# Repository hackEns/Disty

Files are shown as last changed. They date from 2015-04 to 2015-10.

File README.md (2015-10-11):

Disty
=====

Disty is a [hackEns](http://hackens.org) project by [Phyks](http://phyks.me)
and [Elie](http://exppad.com/) aiming at building a low-cost telepresence robot
for videoconference.

More infos can be found on the [project page](http://hackens.org/disty) (in
French). The README and the source code is another good source of
documentation, which should be self-explanatory, in English.

This repo contains all the drawings and code we used to make it work.

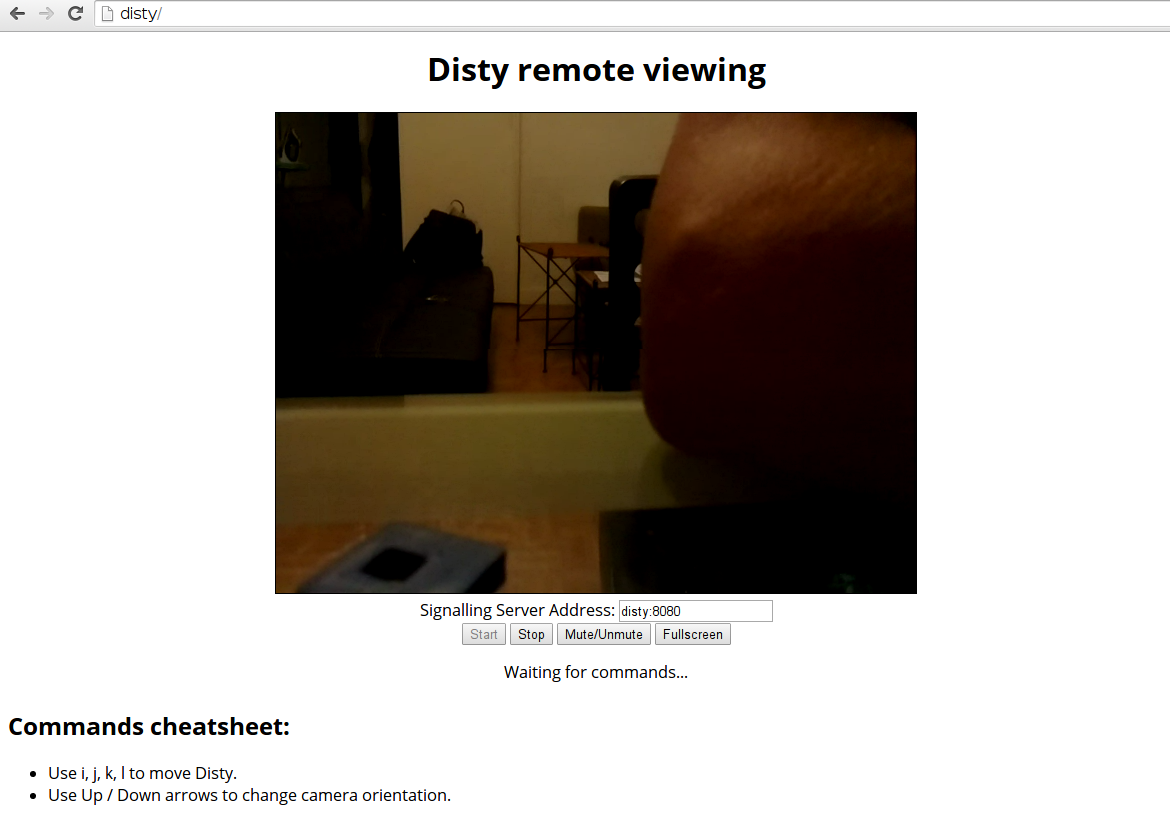
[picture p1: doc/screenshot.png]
Screen capture


<hr/>

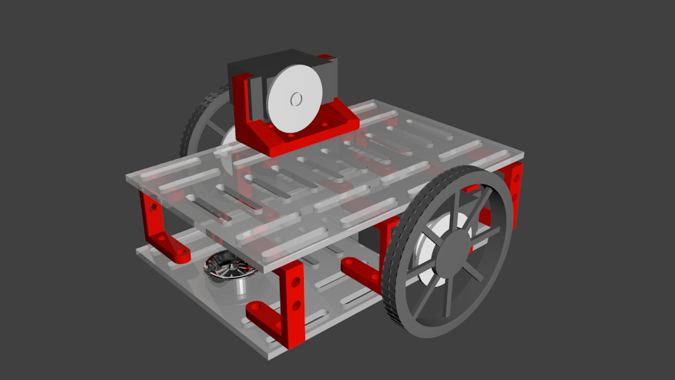
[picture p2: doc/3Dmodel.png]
3D model


<hr/>

Disty

Disty

Disty

## Content of this repo

* `blueprints` contains all the blueprints and drawings for this project.
* `disty` contains the main C++ code, responsible for handling Disty movements
and basic operations.
* `webview` contains the code for the webview, which is the web interface used
to control Disty and display camera (for the remote user).

Note that these folders also contain useful READMEs with more detailed
information on them.

Blueprints are either in `eps` (ready to cut files) or `svg` (working files).
These should be the same and both are provided only to ease usage and
modifications. STL files are ready to print files. They should be included in
the Blender blend files, for easy modifications.

You should laser cut the `top` and `bottom` files for the two main plates.
You should 3D print:
* the `picam_case_*` files for the camera case (licensed under CC BY SA).
* `teleprez.blend` is the complete CAO model of the robot in Blender.
* `camera_servo_holder.stl` is the plastic part to hold the camera servo. You
need to print it once (with a 10,000 scale factor).
* `wheel_servo_holder.stl` is the plastic part to hold the servos for the
wheels. You need four of them (with a 10,000 scale factor).

## Wiring

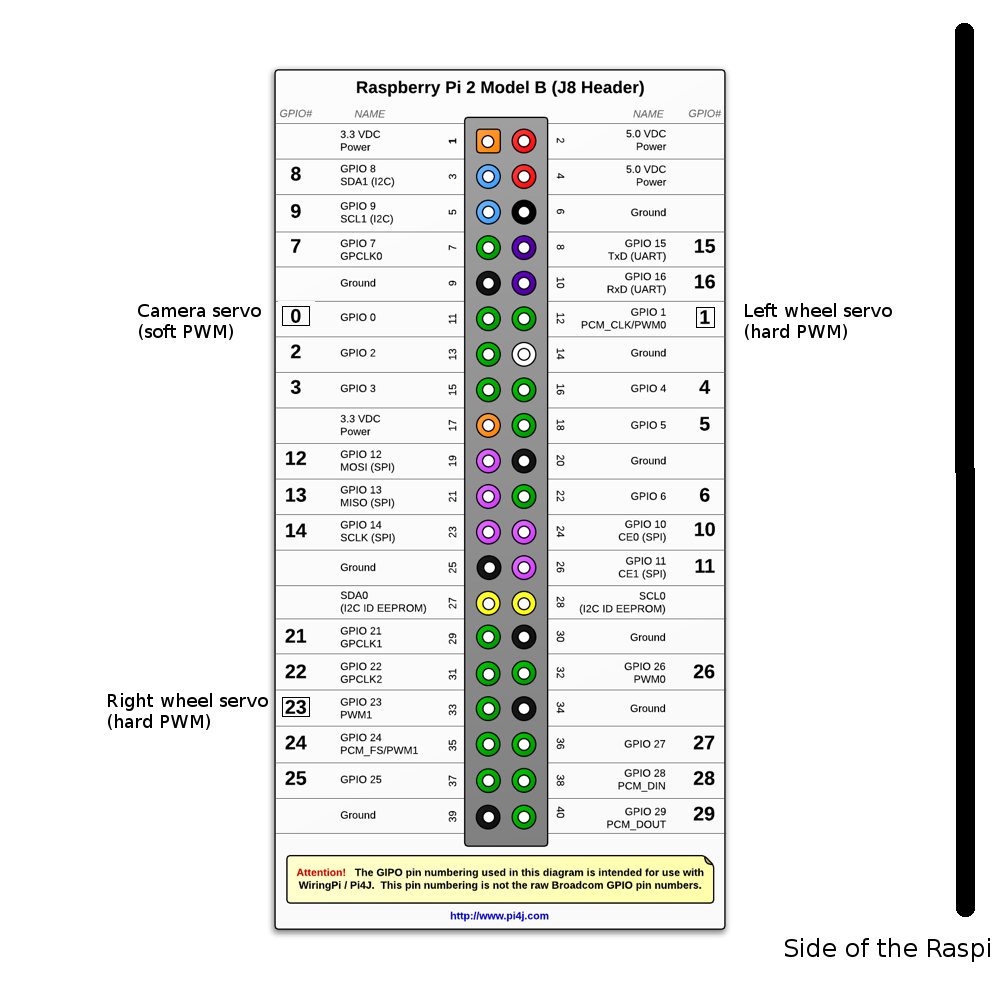
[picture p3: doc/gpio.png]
Wiring


## License

All the source code we wrote is under a beer-ware license, under otherwise specified.

    * --------------------------------------------------------------------------------
    * "THE BEER-WARE LICENSE" (Revision 42):
    * Phyks and Élie wrote this file. As long as you retain this notice you
    * can do whatever you want with this stuff (and you can also do whatever you want
    * with this stuff without retaining it, but that's not cool...). If we meet some
    * day, and you think this stuff is worth it, you can buy us a beer
    * in return.
    *                                                                       hackEns
    * ---------------------------------------------------------------------------------

If you need a more legally valid license, you can consider Disty to be under an MIT license.

## Credits

Thanks https://api.youmagine.com/designs/raspberry-pi-snap-together-camera-case for the camera case (CC BY SA license).

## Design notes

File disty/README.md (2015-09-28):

Main Disty program
==================

This is the main program to handle Disty moves and control.

## Build the software

To build this software, you will need to have [WiringPi](http://wiringpi.com/)
installed system-wide. To use Disty, you will have to have support for GPIOs.

* Create a `build` directory.
* Use CMake to generate Makefiles: `cd build; cmake ..`
* Make: `make`

If you want to tweak the behaviour of the program (such as the used GPIOs),
just edit the `headers/constants.hpp` file.

## Easy test

* Run the program: `cd build; sudo ./disty` (you need to run it as root for PWM
  and GPIO access).
* The server is now listening for commands. Available commands can be found in
  `Robot::listen`. These are `FORWARD`, `BACKWARD`, `STOP` and `KILL`.
* You can use `netcat` on the RaspberryPi to send UDP commands to test it:
  `nc -u localhost 4242`.

## Run the program and control with the webview

Just run the program with `cd build; sudo ./disty` and let it run.

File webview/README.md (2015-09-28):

Disty webview
=============

This is the webview for Disty, to view the camera and control the robot from a web interface.

Note: You can access disty:8080 for a more complete interface provided by uv4l (but not handling moving).

To use this webview, you will need to enable the Raspberry camera module and
install `uv4l` (and its webrtc associated package).

# Starting it

Just run the Python script `run.py` (as root, because it binds port 80) to
serve the web interface on `disty` (if `disty` resolves to your Disty robot)
port 80.

# Tweaking it

To change the keyboard keys, just edit the `js/keyboard.js` file.

# A few notes

This webinterface uses WebRTC (and Google public STUN server for NAT traversal)
to handle video stream. Audio is not yet supported.

It uses a websocket to communicate with the backend code.

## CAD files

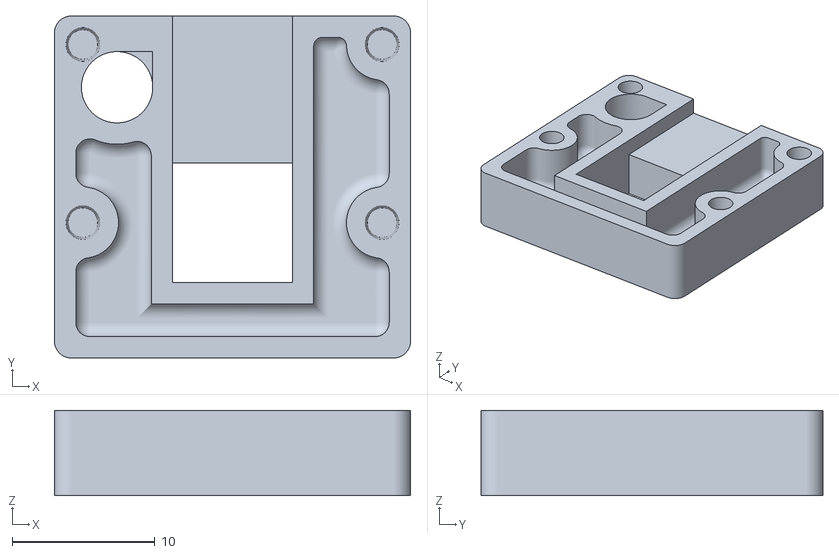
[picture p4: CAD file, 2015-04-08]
blueprints/picam_case_top.stl
25.0 x 24.0 x 6.00

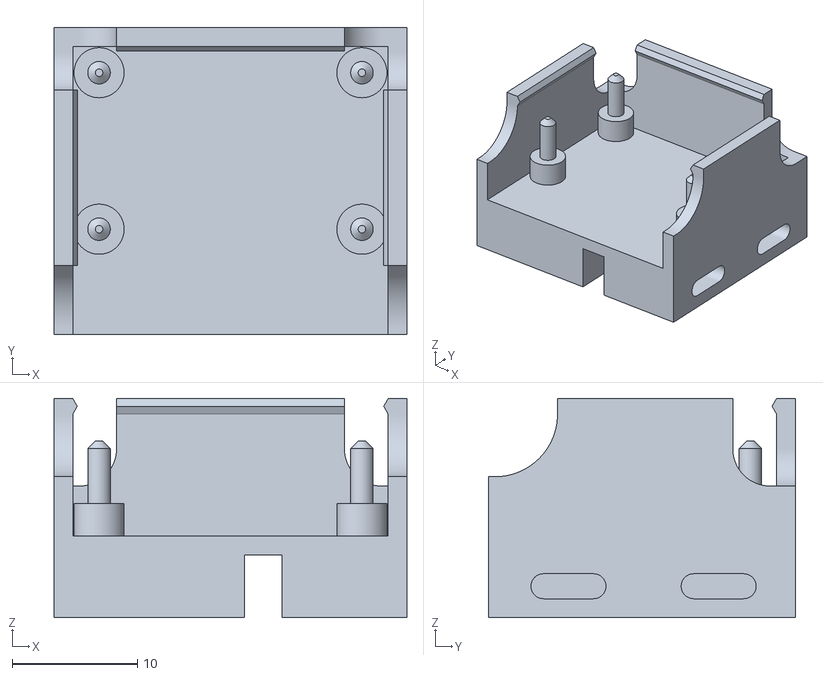
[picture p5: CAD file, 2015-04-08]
blueprints/picam_case_bottom.stl
28.2 x 24.5 x 17.5

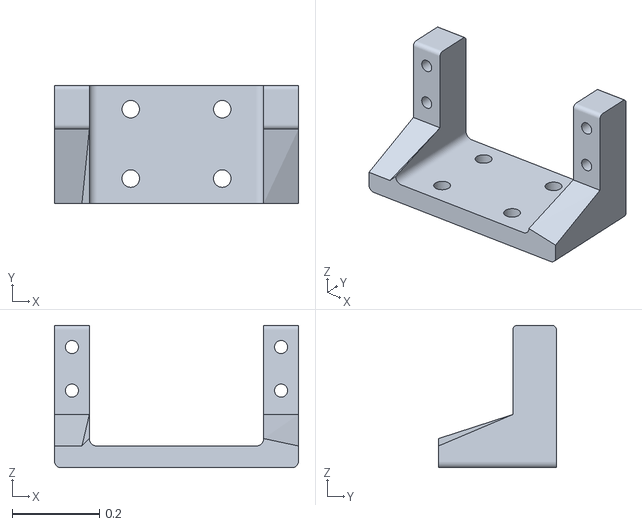
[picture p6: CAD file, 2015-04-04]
blueprints/camera_servo_holder.stl
0.56 x 0.271 x 0.327

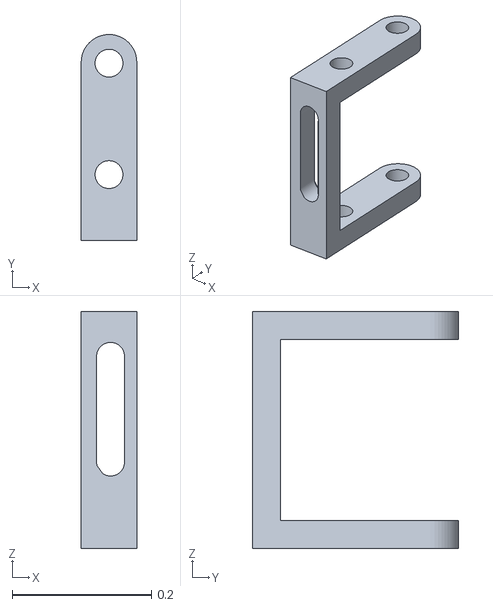
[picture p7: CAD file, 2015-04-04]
blueprints/wheel_servo_holder.stl
0.08 x 0.296 x 0.34

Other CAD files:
blueprints/teleprez.blend

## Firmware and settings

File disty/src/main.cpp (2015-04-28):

#include <arpa/inet.h>
#include <csignal>
#include <cstdlib>
#include <iostream>
#include <netinet/in.h>
#include <sys/socket.h>
#include <wiringPi.h>

#include "constants.hpp"
#include "Robot.hpp"


#include <softPwm.h>
void exitHandler(int signal) {
    // End exit as the client would do, sending "KILL" to local UDP server
    int sock = socket(AF_INET, SOCK_DGRAM, 0);

    struct sockaddr_in servaddr;
    servaddr.sin_family = AF_INET;
    servaddr.sin_addr.s_addr = inet_addr("127.0.0.1");
    servaddr.sin_port = htons(constants::LISTENING_PORT);

    const char buffer[] = "KILL";
    sendto(
            sock,
            buffer,
            sizeof(buffer),
            0,
            (struct sockaddr *) &servaddr,
            sizeof(servaddr));
}


int main(void) {
    // Setup wiringPi with Broadcom pin numbering
    wiringPiSetupGpio();

    // Handle ^C signal
    std::signal(SIGINT, exitHandler);

    robot::Robot disty;

    // Poll commands
    disty.listen();

    return EXIT_SUCCESS;
}

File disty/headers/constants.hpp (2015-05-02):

namespace constants {
    // Max speed allowed, float between 0 and 1
    const float MAX_SPEED = 1.0F;

    // Stop value used in PWM to stop the continuous servo
    const int CONTINUOUS_SERVO_STOP_VALUE = 141;
    // Value to send to PWM to go full forward
    const int CONTINUOUS_SERVO_FULL_FORWARD_VALUE = 155;

    // Minimum position for a standard servo, as PWM
    const int STANDARD_SERVO_MIN_VALUE = 5;
    // Maximum position for a standard servo, as PWM
    const int STANDARD_SERVO_MAX_VALUE = 25;
    // Average standard servo speed, used when using software PWM to prevent
    // jittering. This value is in rounds per seconds.
    const float STANDARD_SERVO_SPEED = 0.75;

    // Pin of the left wheel, Broadcom numbering
    const int LEFT_WHEEL_PIN = 18;
    // Whether this pin is a hard pwm or not
    const bool LEFT_WHEEL_IS_HARD_PWM = true;
    // A float reduction factor used to compensate differences
    // between the wheels
    const float LEFT_WHEEL_REDUCTION_FACTOR = 1.0F;

    // Pin of the right wheel, Broadcom numbering
    const int RIGHT_WHEEL_PIN = 13;
    // Whether this pin is a hard pwm or not
    const bool RIGHT_WHEEL_IS_HARD_PWM = true;
    // A float reduction factor used to compensate differences
    // between the wheels
    const float RIGHT_WHEEL_REDUCTION_FACTOR = 1.0F;

    // Pin for the camera holder, Broadcom numbering
    const int CAMERA_HOLDER_PIN = 17;
    // Whether this pin is a hard PMW or not
    const bool CAMERA_HOLDER_IS_HARD_PWM = false;
    // Software low stop for the camera holder
    const int CAMERA_HOLDER_LOW_STOP = 0;
    // Software high stop for the camera holder
    const int CAMERA_HOLDER_HIGH_STOP = 180;

    // UDP port to listen on
    const int LISTENING_PORT = 4242;
}

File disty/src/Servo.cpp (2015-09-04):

#include <algorithm>
#include <cmath>
#include <stdexcept>
#include <wiringPi.h>
#include <softPwm.h>

#include "Servo.hpp"
#include "utilities.hpp"


namespace servo {
    Servo::Servo(const int pin, const bool is_hard_pwm)
        : pin_(pin), range_(HARD_PWM_RANGE), is_hard_pwm_(is_hard_pwm) {
        if (!is_hard_pwm) {
            range_ = DEFAULT_RANGE_SOFT_PWM;
            pinMode(pin, OUTPUT);
            if (0 != softPwmCreate(pin, 0, range_)) {
                throw std::runtime_error("Unable to initialize Servo.");
            }
        }
        else {
            // Set pin as PWM pin
            pinMode(pin, PWM_OUTPUT);

            // Set PWM correctly
            // Set the PWM mode to Mark:Space which is the standard one
            pwmSetMode(PWM_MODE_MS);
            // Set clock and range prefactor to be as Arduino (tweak frequency)
            pwmSetClock(HARD_PWM_CLOCK);
            pwmSetRange(HARD_PWM_RANGE);
        }

    }

    Servo::~Servo(void) {
        // Set the PWM pin as output and write low to be sure to release PWM signal
        pinMode(pin_, OUTPUT);
        digitalWrite(pin_, LOW);
    }


    int Servo::getPin(void) const {
        return pin_;
    }


    void Servo::writeZeroSoftPWM(void) {
        if (!is_hard_pwm_) {
            softPwmWrite(pin_, 0);
        }
    }


    StandardServo::StandardServo(const int pin, const int min_angle, int max_angle, float average_speed, bool is_hard_pwm)
        : Servo(pin, is_hard_pwm), position_(0), min_angle_(min_angle), max_angle_(max_angle), average_speed_(average_speed)
    {
        // Empty on purpose
    }


    int StandardServo::getPosition(void) const {
        return position_;
    }


    void StandardServo::setPosition(const int position) {
        const int value = static_cast<int>(utilities::clamp(
                (((position / 180.) * (max_angle_ - min_angle_)) +
                 min_angle_),
                min_angle_,
                max_angle_));
        if (is_hard_pwm_) {
            pwmWrite(pin_, value);
        } else {
            softPwmWrite(pin_, value);
            // Let the servo move, based on the passed average speed.
            int delay_milliseconds = static_cast<int>(
                    std::abs(position_ - position) /
                    360.0f /
                    average_speed_ *
                    1000);
            utilities::millisleep(std::max(delay_milliseconds, 10));  // 10ms is the time taken by a PWM cycle of wiringPi
            // Stop the soft PWM signal, to prevent jittering. The servo should
            // hold its position.
            softPwmWrite(pin_, 0);

        }
        position_ = position;
    }



    ContinuousServo::ContinuousServo(const int pin, const int stop_value, const int full_forward_value, const bool is_hard_pwm)
        : Servo(pin, is_hard_pwm), speed_(0), stop_value_(stop_value), full_forward_value_(full_forward_value)
    {
        // Empty on purpose
    }


    ContinuousServo::~ContinuousServo(void)
    {
        setSpeed(0.0F);
    }


    float ContinuousServo::getSpeed(void) const {
        return speed_;
    }


    void ContinuousServo::setSpeed(float speed) {
        speed = utilities::clamp(speed, -1, 1);
        int value = static_cast<int>(
                stop_value_ +
                speed * (full_forward_value_ - stop_value_));
        if (is_hard_pwm_) {
            pwmWrite(pin_, value);
        } else {
            softPwmWrite(pin_, value);
        }
        speed_ = speed;
    }
}  // namespace servo

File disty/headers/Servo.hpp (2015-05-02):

namespace servo {
    const int DEFAULT_RANGE_SOFT_PWM = 50;  // 50Hz

    // These constants are computed so that the base frequency is 20ms (for
    // servos) and the 1.5ms pulse is a valid int multiple. This means:
    // * 19.2 MHz / (CLOCK * RANGE) = 50Hz (19.2MHz being the base frequency of
    // the PWM clock in the raspi).
    // * There exists a valid int such that pwmWrite(pin, INT) is a 1.5ms pulse
    // (which is the stop position, or middle position for standard servo, and
    // servos are supposed to be symmetric with respect to this position).
    const int HARD_PWM_CLOCK = 200;
    const int HARD_PWM_RANGE = 1920;

    // The minimum pulse width is 100µs. If we take a range of 100, this gives
    // us 100 * 100 = 10^4 µs or a frequency of 100Hz. A servo is controlled
    // with 20ms pulses, or a frequency of 50Hz, then the range is 200.
    const int SOFT_PWM_RANGE = 200;


    class Servo {
        public:
            /**
            * Construct a Servo object on specified pin.
            *
            * @param[in] pin is the pin on which the servo is attached.
            * @param[în] is_hard_pwm defines whether the pwm on the pin is hard or not
            */
            Servo(const int pin, const bool is_hard_pwm);
            virtual ~Servo(void);

            /**
            * Get the pin on which the servo is attached.
            */
            int getPin(void) const;

            /**
             * Write zero to the soft PWM. Used for preventing
             * servo jittering once target is reached.
             */
            void writeZeroSoftPWM(void);
        protected:
            int pin_;  /** Servo pin. */
            int range_;  /** Internal range for the PWM. */
            bool is_hard_pwm_;  /** Whether it is a hard PWM pin or not. */
        private:
    };


    class StandardServo : public Servo {
        public:
            /**
            * Construct a StandardServo object on specified pin.
            *
            * @param[in] pin is the pin on which the servo is attached.
            * @param[in] min_angle is the min angle of the servo, expressed in
            *            units of PWM range (and *not* in degrees / rads)
            * @param[in] max_angle is the max angle of the servo, expressed in
            *            units of PWM range (and *not* in degrees / rads)
            * @param[in] average_speed is the average speed of the servo in
            *            rounds per seconds. Used when software PWM is used, to
            *            prevent jittering.
            * @param[în] is_hard_pwm defines whether the pwm on the pin is hard or not
            */
            StandardServo(const int pin, const int min_angle, const int max_angle, const float average_speed, const bool is_hard_pwm);

            /**
            * Get the current servo position.
            */
            int getPosition(void) const;

            /**
            * Move the servo to specified position
            *
            * @param[in] position is the expected position of the servo, in
            *            degrees between 0 and 180.
            */
            void setPosition(const int position);
        protected:
        private:
            int position_;  /** Position of the servo. */
            int min_angle_;  /** Minimal angle of the servo. */
            int max_angle_;  /** Maximal angle of the servo. */
            float average_speed_;  /** Average speed of the servo, in rounds per seconds. */
    };


    class ContinuousServo : public Servo {
        public:
            /**
            * Construct a Servo object on specified pin.
            *
            * @param[in] pin is the pin on which the servo is attached.
            * @param[în] stop_value is the PWM value corresponding to stop (speed = 0)
            * @param[in] full_forward_value is the PWM value corresponding to full
            *            speed forward.
            * @param[în] is_hard_pwm defines whether the pwm on the pin is hard or not
            *
            * @remark full_forward_value and stop_value must take into account the PWM range!
            */
            ContinuousServo(const int pin, const int stop_value, const int full_forward_value, const bool is_hard_pwm);

            /**
            * Stop the servo on destruction.
            */
            ~ContinuousServo(void);

            /**
            * Get the current servo speed.
            * Speed is 1 for full speed forward, and -1 for full speed backward.
            */
            float getSpeed(void) const;

            /**
            * Set the servo speed.
            * Speed is 1 for full speed forward, and -1 for full speed backward.
            */
            void setSpeed(float speed);
        protected:
        private:
            float speed_;  /** Speed of the servo. */
            int stop_value_;  /** PWM value for the stop position of the servo. */
            int full_forward_value_;  /** PWM value for full speed forward. */
    };
}

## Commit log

2015-04-04 Restore blueprints
    [teleprez x4.stl, teleprez.blend, teleprez.stl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]
2015-04-08 Add picam 3D model
    [picam_case_bottom.STL, picam_case_top.STL]
2015-04-08 Fix errors
    * Fix cmake file
    * Now compiles
    * Update Servo class, to be tested
    [Robot.cpp, Servo.cpp, Servo.hpp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]
2015-04-15 Disty working and controlling one servo
    Disty is able to control one wheel, either FORWARD, BACKWARD or STOP. UDPServer and exit is working.
2015-04-17 Fix some stuff with Servos, StandardServo still not working
    [Robot.cpp, Servo.cpp, Servo.hpp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]
2015-04-27 Camera holder is working
2015-05-01 Found a hack to stabilize servo
    [Robot.cpp, Servo.cpp, Servo.hpp]
2015-05-02 Completely solve the jittering problem on camera holder
    [Robot.cpp, Servo.cpp, Servo.hpp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]
2015-05-02 Fix bug in nanosleep
    [Robot.cpp, Servo.cpp]
2015-05-02 Uncomment servo write 0
2015-09-28 Fix wrong function definition in Robot, turning is ok
    [Robot.cpp]
2015-09-28 Documenting a bit more
    [picam_case_bottom.stl, picam_case_top.stl]
2015-09-29 Add note about picamera case
2015-10-10 Document how to print and assemble Disty
    [camera_servo_holder.stl, teleprez.stl, wheel_servo_holder.stl]
2015-10-10 Add scale factor for prints
